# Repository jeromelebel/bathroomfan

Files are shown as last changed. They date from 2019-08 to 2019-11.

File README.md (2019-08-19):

# Quiet Bathroom Fan

## Goal

My goal was to create a bathroom fan that would be very quiet and would be easy to clean. Removing the dust helps to keep the fan quiet.
The fan needed to be speed controlled, so the humidity could be removed quickly after a shower, and the rest of the time the air would not be renewed too fast (to avoid losing heat during winter, to be the quietest possible the rest of the time).

## Description

### Fan

This project started when I found out how quiet a good PC fan can be. So it was obvious for me to use a PC fan for that project. I chose 120mm fan, that size fits perfectly the hole in my bathroom wall.
A PC fan was also a perfect choice because most of the can be controlled with a PWM signal.

One of the concerns could be the humidity and the fan. I don’t think it will be a problem in the long term, since the goal of this project is to remove humidity. If the fan fails too quickly, I will change it for a model that can support more humidity (IP52 or even IP 67).

I went with a Noctua one as it has a good reputation, but other brands would work fine too. It is not clear which model is the best. Of course, the noise and the airflow speed are important parameters, but it seems that the static pressure should be important too (in case the wind tries to blow air in the opposite direction).
The NF-A12x25 PWM or NF-F12 PWM seem to be a good compromises. After testing the NF-F12 PWM, I finally got the NF-f12 PPC-3000 PWM. It looks like the exact same design than NF-F12 PWM, but it can run twice faster.

One important part is that kind of PC fan uses 12V.

### Case

I went for the simplest way to get something that fits exactly the need: 3D printing. I used OpenSCAD software. I know how to use it and that is definitely a good solution for that kind of project.

### Microcontroller

There are a lot of possible choices. I prefered to have a wifi microcontroller, to get temperature and humidity monitoring. That’s definitely not a requirement. Any small arduino like should work fine.
The extra feature was to be able to upload a new firmware without a USB cable. I knew I would adjust a lot the software at the beginning. I wanted to avoid having a USB cable hanging, or worse, having to open and close the fan box too often.
I think the popular ESP32 could be a good choice. But, in the past, I used few Particle Photon, so I used it again for that project.

With most of choices, 5V is needed to power the microcontroller (even if it works in 3.3V for input/output).

### Voltage

The big issue of this project is the voltage. This project has to be connected to 230V. Be aware, this can be very dangerous, and a mistake can be deadly.
Since the fan needs 12V, I chose to get from 230V to 12V, and then convert the 12V into 5V for the microcontroller.
The microcontroller inputs and outputs work in 3.3V. So I used the 3.3V from the microcontroller to power the pull-up resistors and the sensors (like the DHT22).

### Sensors

Of course a humidity sensor is needed. Since it is always easier to add stuff during design, it is better to add extra ones even if it is not useful now. The sensors:
- DHT22
- PIR sensor
- light sensor

The PIR is used to turn off LEDs when nobody is the bathroom. The light sensor is not used so far. All 3 sensors can work in 3.3V.

### LEDs

I knew I would spend time to adjust my software according to the humidity and the fan noise. To avoid having to use my laptop/phone to get values about the fan speed and humidity, I chose to add 8 NeoPixels from Adafruit. The goal is to display those values and have a quick look, so I can understand what is going on.
And also because it looks cool :).

### Components

- 240V to 12V
https://www.amazon.fr/gp/product/B017R4INRI/
- 12V to 5V
https://www.amazon.fr/dp/B07B7KCT44/
- PC Fan
https://www.amazon.fr/gp/product/B00KESS6O0/
- Temperature and humidity sensor
https://www.amazon.fr/Homyl-Dhumidit%C3%A9-Temp%C3%A9rature-Num%C3%A9rique-Adaptateur/dp/B07C9DRHL5/
- Photon particle
https://www.amazon.fr/Particle-PHOTONNOH-Photon-without-Headers/dp/B01BKOVIY6
- PIR sensor
https://www.amazon.fr/COM-four-pyroelektrischer-infrarouge-détecteur-mouvement/dp/B00W7CHFWU
- LDR
https://www.amazon.fr/qualité-Lumière-résistance-dépendant-photorésistance/dp/B00NXW9WZ6
- NeoPixel
https://www.amazon.fr/NeoPixel-Stick-WS2812-Integrated-Drivers/dp/B00KLBTT1E
- Fan filter
https://www.amazon.fr/gp/product/B00DL4BMVS

## 3D Model

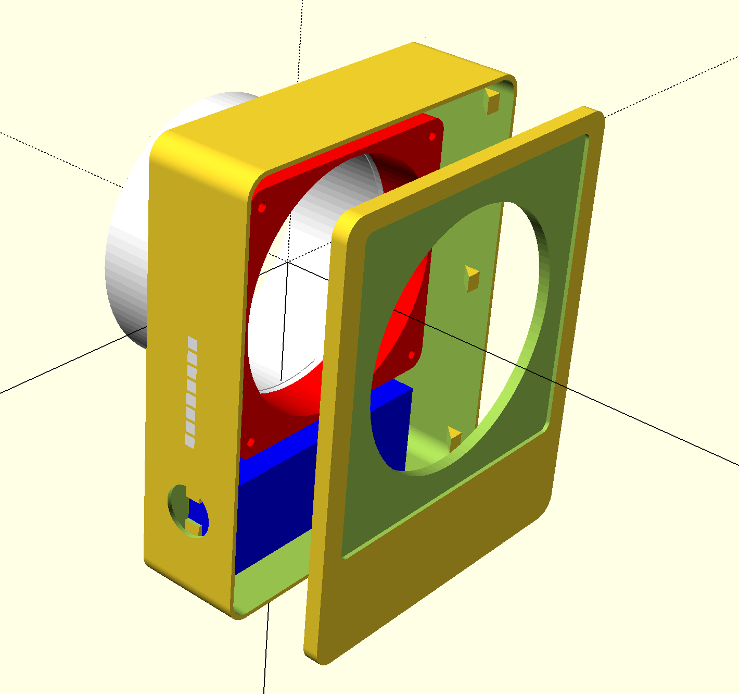
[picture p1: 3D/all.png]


To be able to print correctly the fan case, the model has been divided into 3 pieces: 
- the [pipe](3D/pipe.stl) for the exhaust fan
- the [lid](3D/lid.stl)
- the [case](3D/case.stl) itself
- the [LED windows](3D/LED.stl)

I chose to print the case in 2 colors, white filament, for the main part, and transparent filament for the 8 LED little windows. Those windows are not required. The case is big, but it can be reduced a little. I was able to print it on Ultimaker 3 extended.

The tube and the case have been glued with hot glue so it can be detached later if needed.
I wanted to screw the lid to the case, but it is not useful. I also wanted to use small magnets to keep the filter, but it is not needed either.
Both fit perfectly.

## Schema

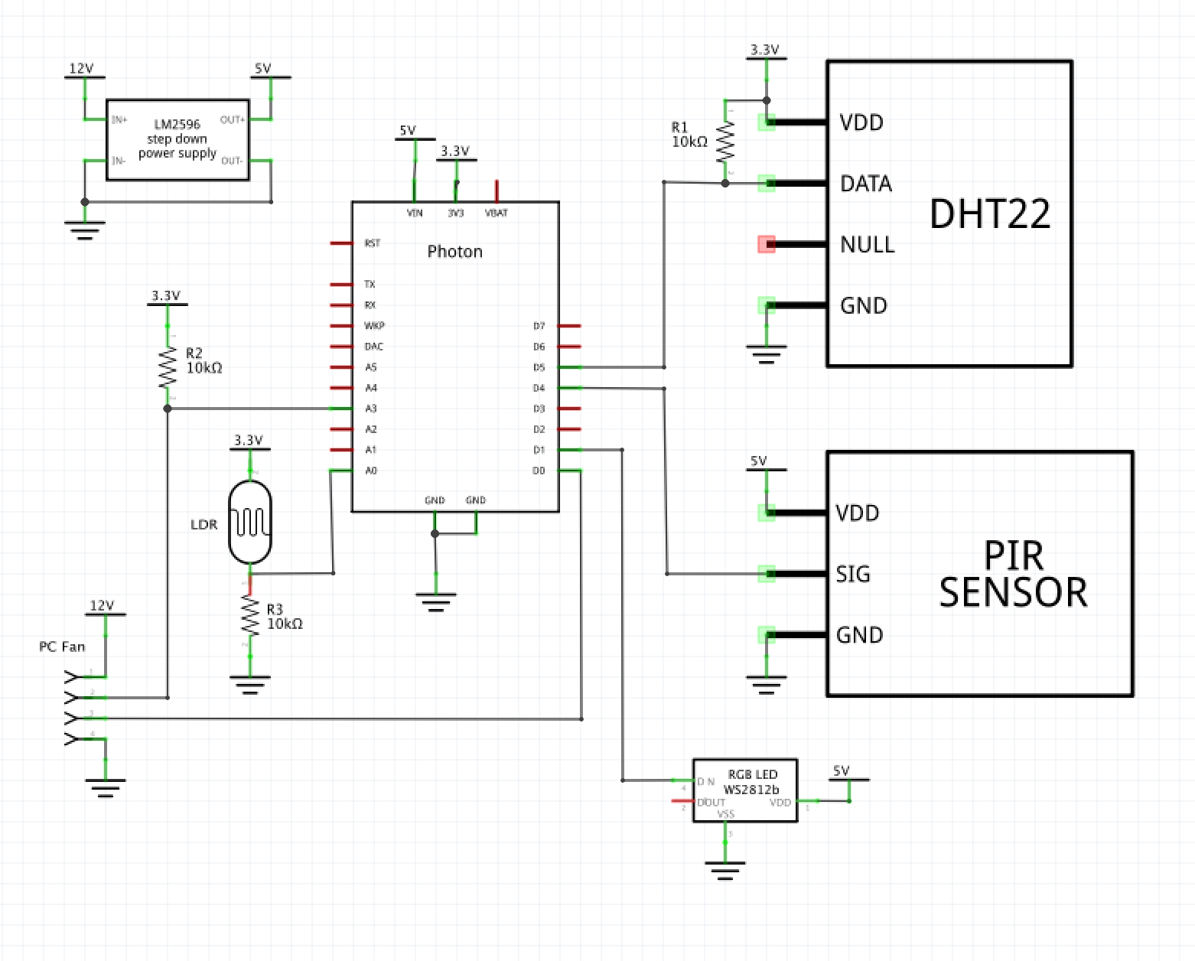
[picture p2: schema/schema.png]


Fan
- PWM connected to D0
- Rotation pin connected to A3 with a pull-up 10k resistor to 3.3V

LDR
- 3.3V
- Pulldown 10k to ground and pin A0

NeoPixel (8 RGB pixels)
- pin: D1

PIR
- pin: D4
DHT 22 (humidity & temperature)
- pin: D5
- Pullup 10k to 3.3V

## Software

The software can be easily updated to have any configuration. So far, I configured my fan to run with the following settings:
- from  0% to  50% of humidity, fan speed is set at 20%
- from 50% to  65% of humidity, fan speed is set at 40%
- from 65% to 100% of humidity, fan speed is set at 75%

When the PIR sensor detects something, the LEDs are turned on. First the LEDs shows, in green color, the temperature, during 5 seconds. Between 20 and 28 Celsius, LEDs are turned on from bottom to top, with one LED per degres. Between 12 and 20 Celsius, LEDs are turned off from bottom to top with one LED per degres.

By default, the LEDs always shows, in red color, the humidity (range from 10% to 100%). If the PIR sensor detects nothing during 5mn the LEDs are turned off.

While the LEDs are on, if the fan speed changes, the LEDs shows, in white color, the fan speed (range from 10% to 100%), during 0.5s.

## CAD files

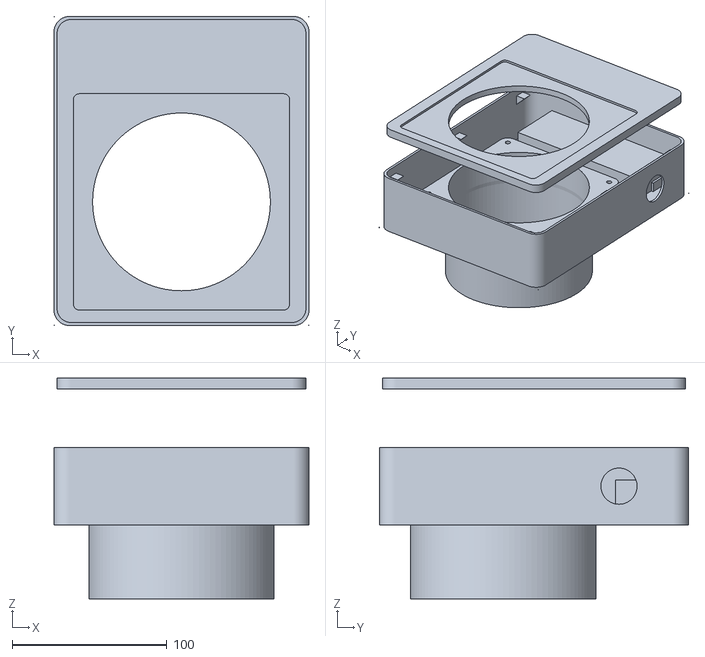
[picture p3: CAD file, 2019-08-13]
3D/all.stl
165.0 x 200.0 x 143.0

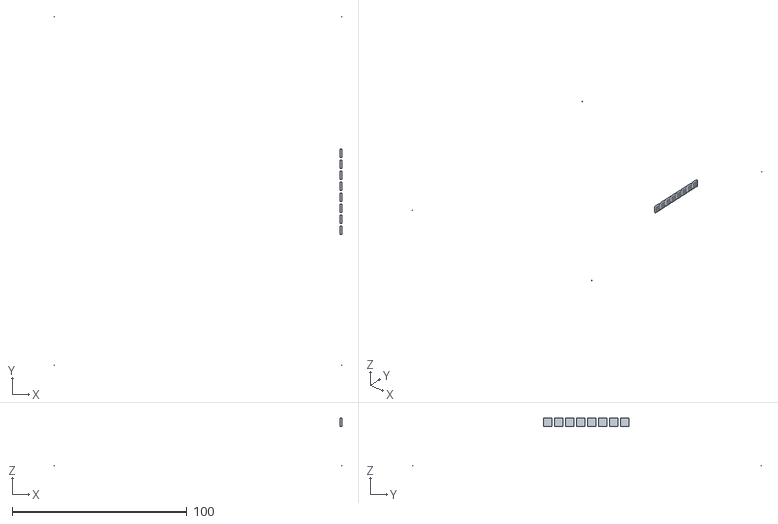
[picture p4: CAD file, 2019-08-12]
3D/LED.stl
165.0 x 200.0 x 27.5

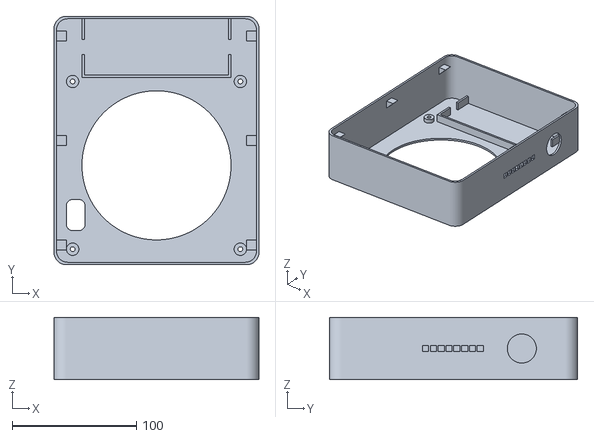
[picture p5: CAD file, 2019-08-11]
3D/case.stl
165.0 x 200.0 x 50.0

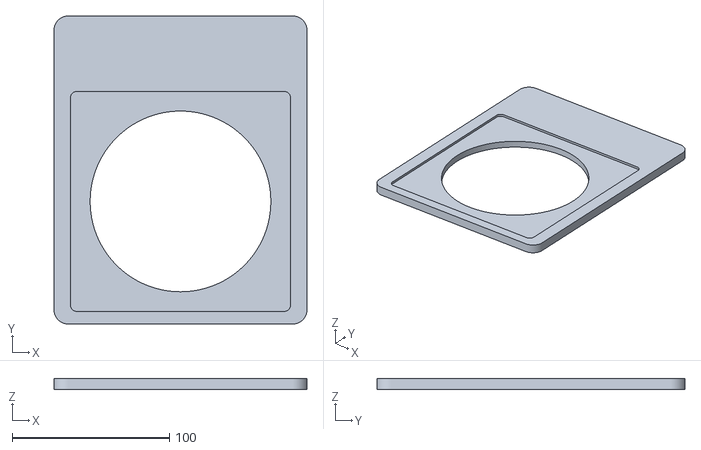
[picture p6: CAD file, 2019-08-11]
3D/lid.stl
161.0 x 196.0 x 7.00

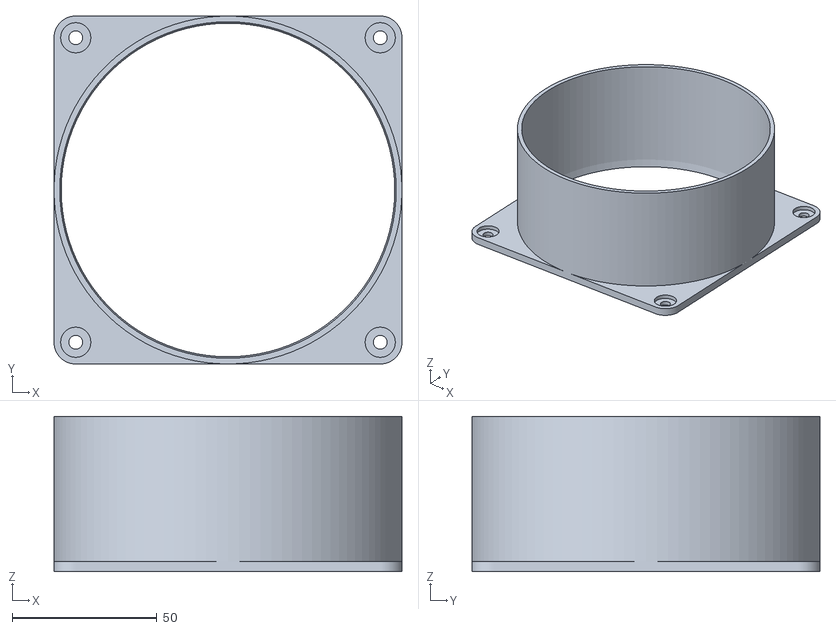
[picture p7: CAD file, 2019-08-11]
3D/pipe.stl
120.0 x 120.0 x 53.6

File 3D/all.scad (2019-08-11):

include <VMC.scad>

union() {
  union() {
    case(true);
    only_led();
  }
  translate([0, 0, wall + pipe_lid_wall])
    rotate([180, 0, 0])
      pipe(true);
  translate([0, 0, case_height - wall + 40]) lid();
}

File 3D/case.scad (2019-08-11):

include <VMC.scad>

case(false);

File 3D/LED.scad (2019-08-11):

include <VMC.scad>

only_led();

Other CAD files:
3D/lid.scad
3D/VMC.scad
3D/pipe.scad

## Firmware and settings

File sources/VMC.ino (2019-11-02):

#include <Particle.h>

#include "DHTController.h"
#include "FanController.h"
#include "LEDController.h"
#include "LightController.h"
#include "MQTTController.h"
#include "NightModeController.h"
#include "PIRController.h"
#include "PreferenceController.h"

#define ShowTemperatureDelay   5000
#define MQTTServerPref         "mqtts"
#define MQTTPortPref           "mqttp"
#define DSTOffsetPref          "dst"
#define TempMQTTTopic          "vmc/temp"
#define HumiMQTTTopic          "vmc/humi"
#define FanRPMMQTTTopic        "vmc/fan/rpm"
#define FanSpeedMQTTTopic      "vmc/fan/speed"
#define LocalTimeZone          2
#define DaylightSavingTimeZone 1
#define NightMaxFanSpeed       70

DHTController dhtController;
FanController fanController;
LEDController ledController;
LightController lightController;
MQTTController mqttController;
NightModeController nightModeController;
PIRController pirController;
PreferenceController preferenceController;

int fanSpeedOverride = -1;
int counter = 0;
int loopDuration = 0;
String startTime;
LEDController::PixelColors lastFanSpeedNotification = LEDController::PixelColors::black();

typedef struct {
  int humidity;
  int speed;
} HumidityFanSpeed;

HumidityFanSpeed humidityFanSpeed[] = {
  {  40,  20 }, // for  40% humidity:  20% fan speed.
  {  50,  40 }, // for  50% humidity:  40% fan speed.
  {  80, 100 }, // for  80% humidity: 100% fan speed.
  { 100, 100 }, // for 100% humidity: 100% fan speed.
};
const size_t humidityFanSpeedCount = sizeof(humidityFanSpeed) / sizeof(*humidityFanSpeed);

String valueForTopic(String topic) {
  if (topic == TempMQTTTopic) {
    return String(dhtController.getTemperature(), 1);
  } else if (topic == HumiMQTTTopic) {
    return String(dhtController.getHumidity(), 1);
  } else if (topic == FanRPMMQTTTopic) {
    return String(fanController.getRPM());
  } else if (topic == FanSpeedMQTTTopic) {
    return String(fanController.getFanSpeed());
  }
  return String();
}

void showTemperatureNotification(double temperature) {
  LEDController::PixelColors pixelColors = LEDController::PixelColors::black();
  uint32_t color = 0x000100;
  if (temperature >= 20.5) {
    pixelColors = LEDController::PixelColors::percentageValue(temperature, 19.5, 28.5, color);
  } else if (temperature < 19.5) {
    pixelColors = LEDController::PixelColors::percentageValue(temperature, 20.5, 11.5, color);
  } else {
    pixelColors = LEDController::PixelColors::values(0b10000001, color);
  }
  LEDController::Notification notification(pixelColors, ShowTemperatureDelay);
  ledController.addNotification(notification);
}

void setFanSpeedForHumidity(double humidity) {
  size_t index = 0;
  for (; index < humidityFanSpeedCount; index++) {
    if (humidity <= humidityFanSpeed[index].humidity) {
      break;
    }
  }
  if (index == 0) {
    setFanSpeed(humidityFanSpeed[index].speed);
    return;
  }
  double previousLevelHumidity = humidityFanSpeed[index - 1].humidity;
  double humidityDelta = humidityFanSpeed[index].humidity - previousLevelHumidity;
  int previousLevelFanSpeed = humidityFanSpeed[index - 1].speed;
  int fanSpeedDelta = humidityFanSpeed[index].speed - previousLevelFanSpeed;
  int fanSpeed = (humidity - previousLevelHumidity) / humidityDelta * fanSpeedDelta + previousLevelFanSpeed;
  setFanSpeed(fanSpeed);
}

void syncTimeIfNeeded() {
  unsigned long lastSync = Particle.timeSyncedLast();
  if (millis() - lastSync > 24 * 60 * 60 * 1000) {
    Particle.syncTime();
  }
}

void setup() {
  Serial.begin(115200);
  WiFi.setHostname("VMC");
  startTime = Time.timeStr();

  preferenceController.load();

  dhtController.begin();
  fanController.begin();
  ledController.begin();
  lightController.begin();
  nightModeController.begin();
  pirController.begin();

  Particle.function("SetMQTTServer", setMQTTServer);
  Particle.function("SetMQTTPort", setMQTTPort);
  Particle.function("SetDST", setDSTOffset);
  Particle.function("DST", getDSTOffset);
  Particle.function("fanspeed", setFanSpeedOverride);
  Particle.function("test", myTestMethod);
  Particle.variable("loop", loopDuration);
  Particle.variable("start", startTime);

  String mqttServer = preferenceController.valueForKey(MQTTServerPref);
  String mqttPort = preferenceController.valueForKey(MQTTPortPref);
  Particle.publish("mqtt server", mqttServer, PRIVATE);
  Particle.publish("mqtt port", mqttPort, PRIVATE);
  if (mqttServer != "" && mqttPort != "") {
    mqttController.begin(mqttServer, mqttPort.toInt());
    mqttController.addTopic(HumiMQTTTopic, valueForTopic);
    mqttController.addTopic(TempMQTTTopic, valueForTopic);
    mqttController.addTopic(FanRPMMQTTTopic, valueForTopic);
    mqttController.addTopic(FanSpeedMQTTTopic, valueForTopic);
  }
  Time.zone(LocalTimeZone);
  String daylightSavingOffset = preferenceController.valueForKey(DSTOffsetPref);
  Particle.publish("DSTOffset", daylightSavingOffset, PRIVATE);
  Time.setDSTOffset(daylightSavingOffset.toInt());
  nightModeController.setPIRController(&pirController);

  welcomeAnimation();
  dhtController.loop();
  showTemperatureNotification(dhtController.getTemperature());
}

void loop() {
  unsigned long start = micros();

  dhtController.loop();
  fanController.loop();
  ledController.loop();
  lightController.loop();
  mqttController.loop();
  nightModeController.loop();
  pirController.loop();

  int humidity = dhtController.getHumidity();
  setFanSpeedForHumidity(humidity);
  if (pirController.isHumanPresent()) {
    ledController.setPixels(LEDController::PixelColors::percentageValue(dhtController.getHumidity(), 10, 100, 0x010000));
    if (!ledController.isOn()) {
        showTemperatureNotification(dhtController.getTemperature());
        ledController.setOn(true);
    }
  } else {
    ledController.setOn(false);
  }
  syncTimeIfNeeded();
  loopDuration = micros() - start;
}

void welcomeAnimation() {
  ledController.setOn(true);
  int value = 0x0;
  for (int i = 0; i < PIXEL_COUNT; i++) {
    int currentPixel = 0b100000000;
    for (int j = 0; j < PIXEL_COUNT - i; j++) {
      currentPixel = currentPixel >> 1;
      ledController.setPixels(LEDController::PixelColors::values(value | currentPixel, 0x010101));
      delay(50);
    }
    value = value | currentPixel;
  }
  delay(500);
}

void setFanSpeed(int value) {
  if (fanSpeedOverride != -1) {
    return;
  }
  if (nightModeController.isNight() && value > NightMaxFanSpeed) {
    value = NightMaxFanSpeed;
  }
  if (fanController.getFanSpeed() != value && !ledController.hasNotification() && ledController.isOn()) {
    LEDController::PixelColors color = LEDController::PixelColors::percentageValue(value, 10, 100, 0x010101);
    if (color != lastFanSpeedNotification) {
      ledController.addNotification(LEDController::Notification(color, 500));
      lastFanSpeedNotification = color;
    }
  } else {
    lastFanSpeedNotification = LEDController::PixelColors::black();
  }
  fanController.setFanSpeed(value);
}

int setMQTTServer(String server) {
  preferenceController.setValueForKey(server, MQTTServerPref);
  preferenceController.save();
  return 1;
}

int setMQTTPort(String port) {
  preferenceController.setValueForKey(port, MQTTPortPref);
  preferenceController.save();
  return 1;
}

int setDSTOffset(String dst) {
  preferenceController.setValueForKey(dst, DSTOffsetPref);
  preferenceController.save();
  Time.setDSTOffset(dst.toInt());
  return dst.toInt();
}

int getDSTOffset(String notused) {
  return Time.getDSTOffset();
}

int setFanSpeedOverride(String value) {
  fanSpeedOverride = value.toInt();
  if (fanSpeedOverride < 0) {
    fanSpeedOverride = -1;
    return fanSpeedOverride;
  }
  ledController.addNotification(LEDController::Notification(LEDController::PixelColors::percentage(fanSpeedOverride, 0x010101), 500));
  fanController.setFanSpeed(fanSpeedOverride);
  return fanSpeedOverride;
}

int myTestMethod(String stringValue) {
  setFanSpeed(stringValue.toInt());
  return 1;
}

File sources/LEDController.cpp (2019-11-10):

#include "LEDController.h"

#include <neopixel.h>
#include <Particle.h>
#include <vector>

#define PIXEL_PIN D1
#define PIXEL_TYPE WS2812B

// static
LEDController::PixelColors LEDController::PixelColors::percentage(float percentage, uint32_t color) {
  std::vector<uint32_t> colors;
  bool allOff = false;
  bool negatif = percentage < 0;
  percentage = negatif ? -percentage : percentage;
  for (int i = 0; i < PIXEL_COUNT; i++) {
    uint32_t pixelColor = 0x0;
    if (percentage >= (float)(i + 1) / (float)(PIXEL_COUNT + 1)) {
      pixelColor = color;
    } else if (i == 0) {
      allOff = true;
    }
    if (allOff) {
      if (i == PIXEL_COUNT - 1 || i == 0) {
        pixelColor = color;
      } else {
        pixelColor = 0x0;
      }
    }
    if (negatif) {
      colors.insert(colors.begin(), pixelColor);
    } else {
      colors.push_back(pixelColor);
    }
  }
  return LEDController::PixelColors(colors);
}

// static
LEDController::PixelColors LEDController::PixelColors::percentageValue(float value, float minimum, float maximum, uint32_t color) {
  float percentage = 0;
  if (minimum < maximum) {
    if (value < minimum) {
      value = minimum;
    } else if (value > maximum) {
      value = maximum;
    }
    percentage = (value - minimum) / (maximum - minimum);
  } else if (minimum > maximum) {
    if (value > minimum) {
      value = minimum;
    } else if (value < maximum) {
      value = maximum;
    }
    percentage = (value - minimum) / (minimum - maximum);
  } else {
    percentage = 0;
  }
  return LEDController::PixelColors::percentage(percentage, color);
}

// static
LEDController::PixelColors LEDController::PixelColors::values(int pixels, uint32_t color) {
  std::vector<uint32_t> colors;
  for (int i = 0; i < PIXEL_COUNT; i++) {
    colors.push_back((pixels & 1) ? color : 0x0);
    pixels = pixels >> 1;
  }
  return LEDController::PixelColors(colors);
}

// static
LEDController::PixelColors LEDController::PixelColors::black() {
  return values(0, 0);
}

LEDController::PixelColors::PixelColors(std::vector<uint32_t> colors) :
    _pixelColors(colors) {
}

LEDController::PixelColors::~PixelColors() {
}

LEDController::Notification::Notification(LEDController::PixelColors colors, long duration) :
    _duration(duration),
    _startDate(0),
    _started(false),
    _pixelColors(colors) {
}

LEDController::Notification::~Notification() {
}

LEDController::LEDController() :
    _strip(new Adafruit_NeoPixel(PIXEL_COUNT, PIXEL_PIN, PIXEL_TYPE)),
    _defaultPixelColors(LEDController::PixelColors::black()),
    _on(false)  {
}

LEDController::~LEDController() {
  delete _strip;
}

void LEDController::begin() {
  _strip->begin();
  _strip->show();
}

void LEDController::loop() {
  bool needUpdate = false;
  while (!_notifications.empty()) {
    Notification &currentNotification = _notifications[0];
    if (!currentNotification.isStarted()) {
      currentNotification.start();
      needUpdate = true;
      break;
    } else if (currentNotification.hasExpired()) {
      removeCurrentNotification();
      needUpdate = true;
    }
  }
  if (needUpdate) {
    updatePixelColors();
  }
}

void LEDController::setOn(bool value) {
  if (value == _on) {
    return;
  }
  _on = value;
  updatePixelColors();
}

void LEDController::setPixels(const PixelColors &pixelColors) {
  if (_on && !hasNotification()) {
    applyPixelColors(pixelColors);
  }
  _defaultPixelColors = pixelColors;
}

void LEDController::updatePixelColors() {
  if (hasNotification()) {
    applyPixelColors(_notifications[0].pixelColors());
  } else if (_on) {
    applyPixelColors(_defaultPixelColors);
  } else {
    applyPixelColors(LEDController::PixelColors::black());
  }
}

void LEDController::applyPixelColors(const PixelColors &pixelColors) {
  for (int i = 0; i < PIXEL_COUNT; ++i) {
    _strip->setPixelColor(PIXEL_COUNT - 1 - i, pixelColors[i]);
  }
  _strip->show();
}

void LEDController::addNotification(LEDController::Notification notification) {
  _notifications.push_back(notification);
}

void LEDController::startNextNotification() {
}

void LEDController::removeCurrentNotification() {
  if (_notifications.empty()) {
    return;
  }
  _notifications.erase(_notifications.begin());
}

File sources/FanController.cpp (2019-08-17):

#include "FanController.h"

#include <Particle.h>

#define PWM_PIN D0
#define RPM_PIN A3
#define PWM_FREQ 25000

static volatile unsigned long lastRPMChange = 0;
static volatile unsigned long rpmDuration = 0;

void rpmInterrupt() {
  unsigned long currentMicros = micros();
  rpmDuration = currentMicros - lastRPMChange;
  lastRPMChange = currentMicros;
}

FanController::FanController() {
}

FanController::~FanController() {
}

void FanController::begin() {
  pinMode(PWM_PIN, OUTPUT);
  pinMode(RPM_PIN, INPUT);
  attachInterrupt(RPM_PIN, rpmInterrupt, RISING);
  setFanSpeed(0);
  Particle.variable("rpm", _rpm);
  Particle.variable("fanspeed", _fanSpeed);
}

void FanController::loop() {
  readRPM();
}

void FanController::setFanSpeed(int value) {
  if (value < 0) {
    value = 0;
  } else if (value > 100) {
    value = 100;
  }
  _fanSpeed = value;
  analogWrite(PWM_PIN, _fanSpeed / 100. * 255., PWM_FREQ);
}

void FanController::readRPM() {
  if ((unsigned long)(micros() - lastRPMChange) > 200000) {
    _rpm = 0;
  } else {
    _rpm = 1000000. / rpmDuration * 15. * 2.;
  }
}

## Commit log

2019-08-11 Adding schema
    [VMC.fzz]
2019-08-11 Adding 3D model
    [LED.scad, VMC.scad, all.scad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]
2019-08-11 Fixing issue with LM2596
    [VMC.fzz]
2019-08-11 Adding stl files
    [case.stl, lid.stl, pipe.stl]
2019-08-11 Adding STL file links
2019-08-12 Adding LED.stl file
    [LED.stl]
2019-08-13 Adding all.stl (just to have a view of everything)
    [all.stl]
2019-08-13 Updating the fan choice
2019-08-13 Changing fan speed type from double to int
2019-08-13 Nicer code to set the fan speed according to the humidity
2019-08-13 Fixing issue when the humidity is at 100%
    [VMC.ino]
2019-08-17 Showing the temperature notification during 5s
2019-08-17 Changing the fan controller interruption from CHANGE to RISING to be able to measure a more accurate value
2019-08-18 Fixing the limit between pixels for a color value with a percentage
    [LEDController.cpp, VMC.ino]
2019-08-18 Set myTestMethod() to test the temperature
2019-08-18 Showing temperature from 12 to 28 Celsius
2019-08-18 Fixing the fan speed notification
    [VMC.ino]
2019-08-18 Fixing warning to convert an int from signed to unsigned
    [VMC.ino]
2019-08-19 Rounding the temperature more accurately
2019-09-14 Make fan speed progressive
2019-09-14 Update the fan speed notification only when the color really changes
2019-10-18 Fixing the humidity/fan speed conversion
    [VMC.ino]
2019-11-10 Fixing temperature display when below 20
    [LEDController.cpp]
